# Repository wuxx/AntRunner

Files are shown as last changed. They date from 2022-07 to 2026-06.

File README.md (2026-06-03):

# AntRunner
[中文](./README_cn.md)
 * [Introduce](#introduce)
 * [Feature](#feature)
 * [Specification](#specification)
 * [How to Use](#how-to-use)
 * [System Detail](#system-detail)
    * [Gpredict](#gpredict)
    * [Hamlib](#hamlib)
    * [Look4Sat](#look4sat)
    * [SDR#](#sdr)
 * [How to Get One](#how-to-get-one)
 * [Reference](#reference)

## Introduce
AntRunner is a portable antenna rotator designed and made by MuseLab(Another model we designed is the [AntRunner-Pro](https://github.com/wuxx/AntRunner-Pro), which is suitable for fixed installation and long-term operation). It can be used for real-time automatic racking of satellites with corresponding open source software which is available on Windows/Linux/Mac/RaspberryPi/Android. The rotator and the host computer can communicate via wired (serial port) or wireless (Wifi 2.4G).  It can install various types of antennas (usually Yagi antennas), support 360-degree azimuth and 180-degree elevation control, and can support antennas up to 5KG.  It can be powered by a 12V battery or by a fast charging power bank with a 12V fast charging trigger cable. It’s easy to carry as its weight is relatively light and very convenient to use in the wild for HAM.

AntRunner-1
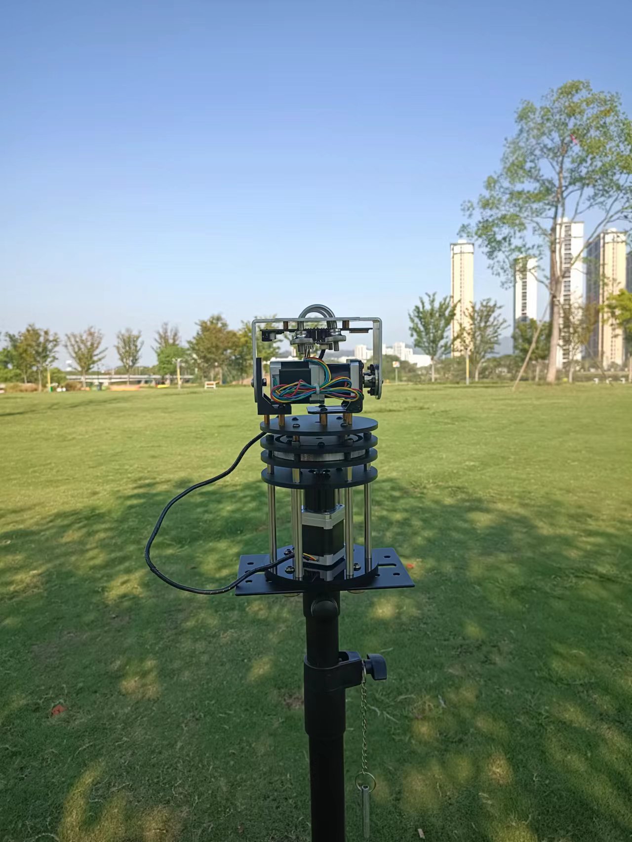
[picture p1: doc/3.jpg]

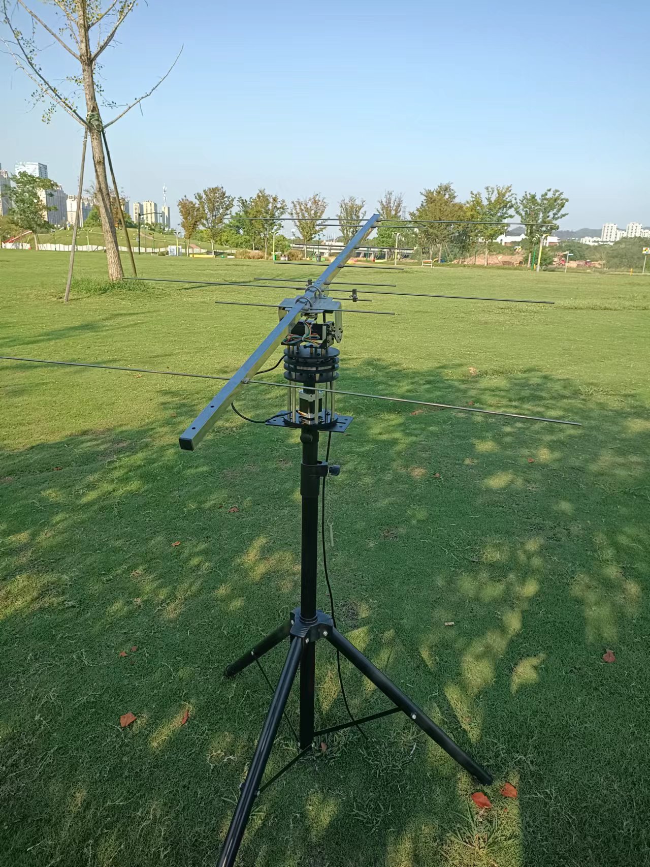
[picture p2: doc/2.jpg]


## Feature
- full Azimuth and elevation angle tracking
- Support Windows/Linux/RaspberryPi/Android
- Support wired serial port control
- Support wireless WiFi 2.4G control
- 12V power supply, convenient for field erection
- Easy disassembly and assembly

## Specification
- Rotation Limit: AZ: 0 - 360°; EL: 0-180°
- Max Load: 5KG
- Backlash: AZ:1° EL:1°
- Weight: 3KG
- Rotator Diameter x Height:  120mmØ x 65mm (H)
- Support Material: 5mm/10mm Acrylic

## How to Use

### Windows

#### 0 Antenna installation
Install the antenna on the U-shaped bracket of the rotator through the U-shaped hoop, and pay attention to install it at the center of gravity of the antenna to make the operation more stable.

#### 1 Rotator adjustment
Before powering on, you need to adjust the azimuth of the rotator to true north (azimuth angle of 0 degrees), and the pitch to be horizontal (pitch angle of 0 degrees). This step can be adjusted through the mobile compass APP.

#### 2 Power up
Use the 12V power supply to power on the rotator, and connect the rotator and PC through the TYPE-C cable. After the normal connection, a serial port will appear in the device manager, as shown in the figure.
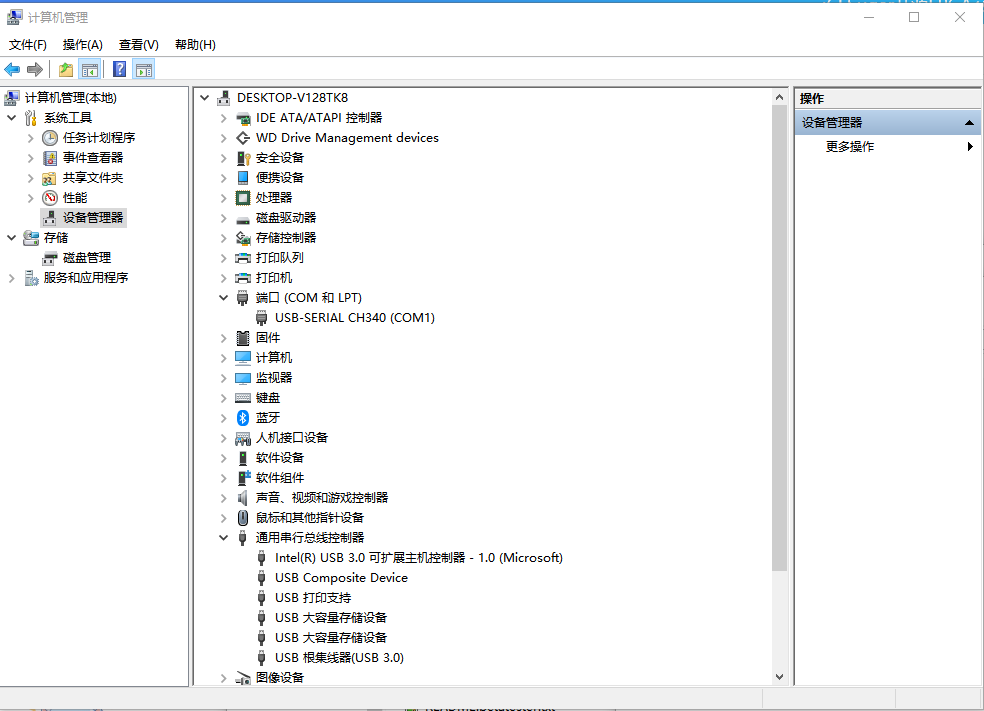
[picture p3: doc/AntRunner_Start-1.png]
AntRunner-1


#### 3 Start Hamlib
Enter the Hamlib directory, there is a batch script in the directory, and the script is a command, as shown below, you need to manually edit the script to modify the serial port number. Since the serial port number is assigned by the system, the serial number is different for different systems, so you need to use a text editor to manually change the serial port number before running.
```
rotctld.exe -vvvvv -m 2401 -r COMx
```
Modify COMx to the actual serial port number that appears in the device manager, save the script, and double-click to run it.
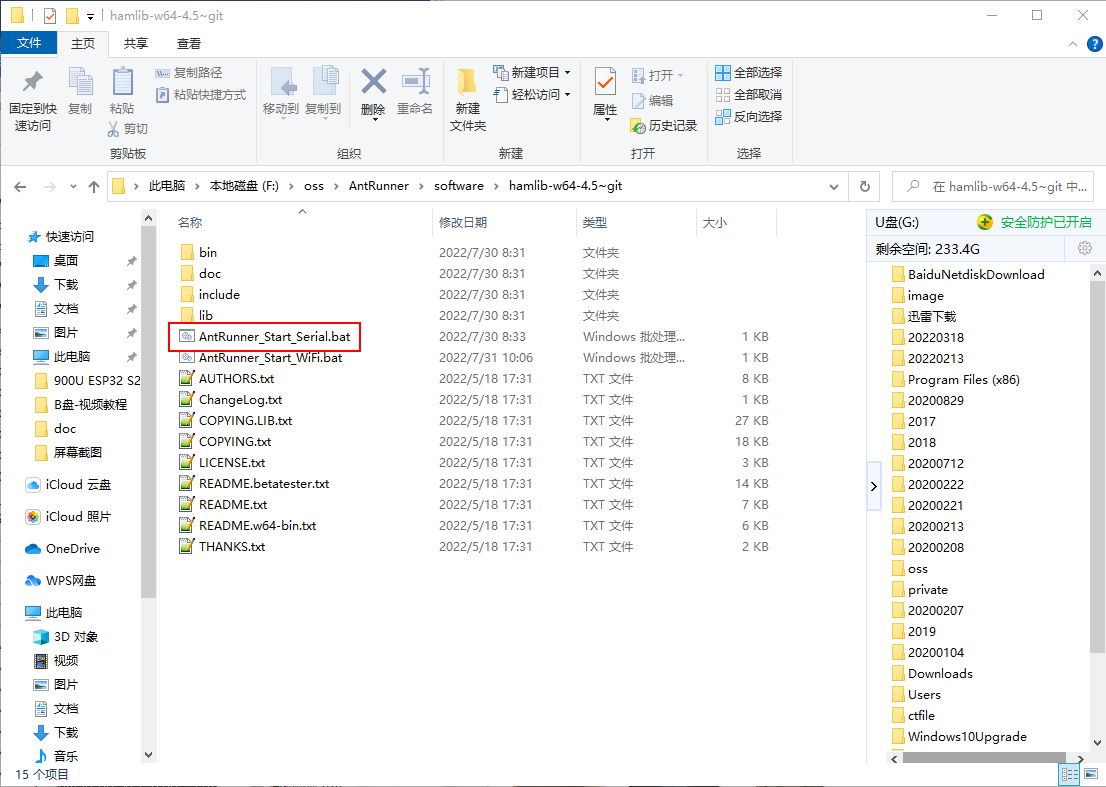
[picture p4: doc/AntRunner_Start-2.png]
AntRunner-2

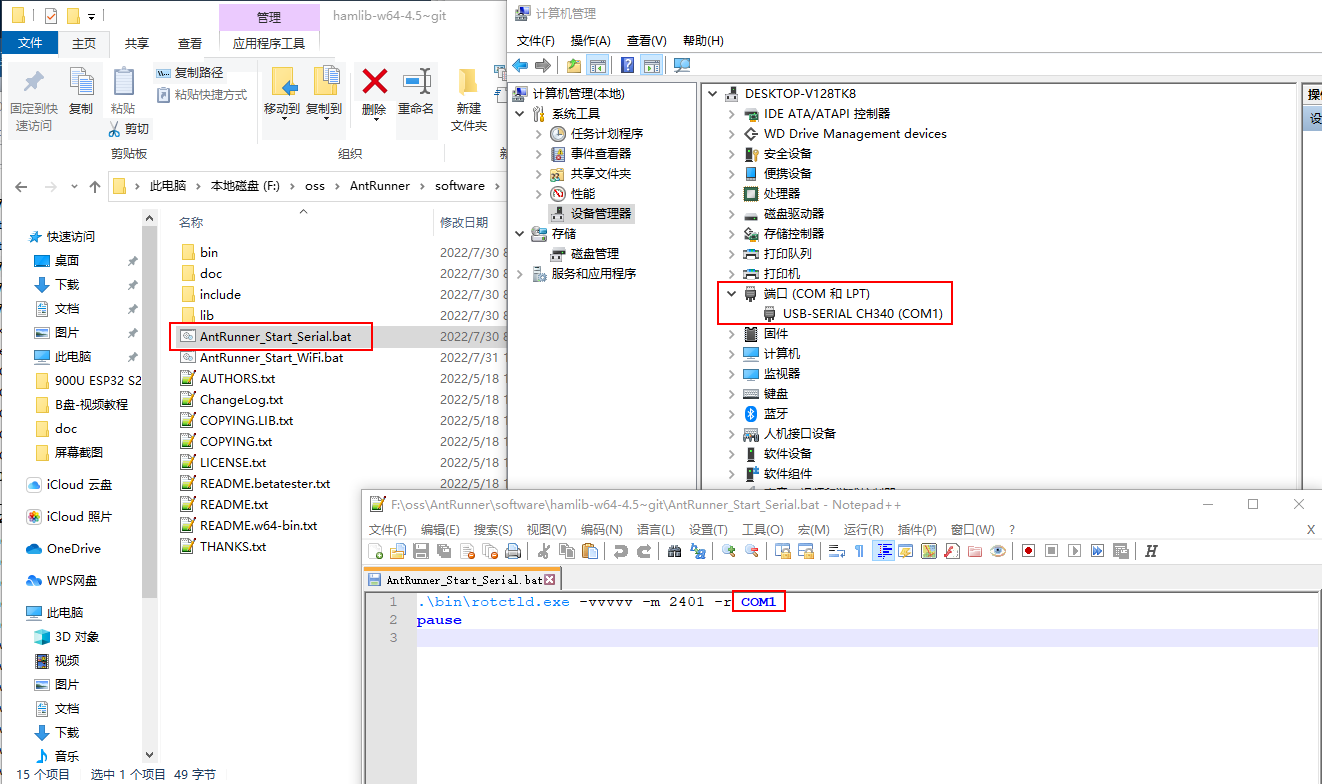
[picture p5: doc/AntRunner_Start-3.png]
AntRunner-3

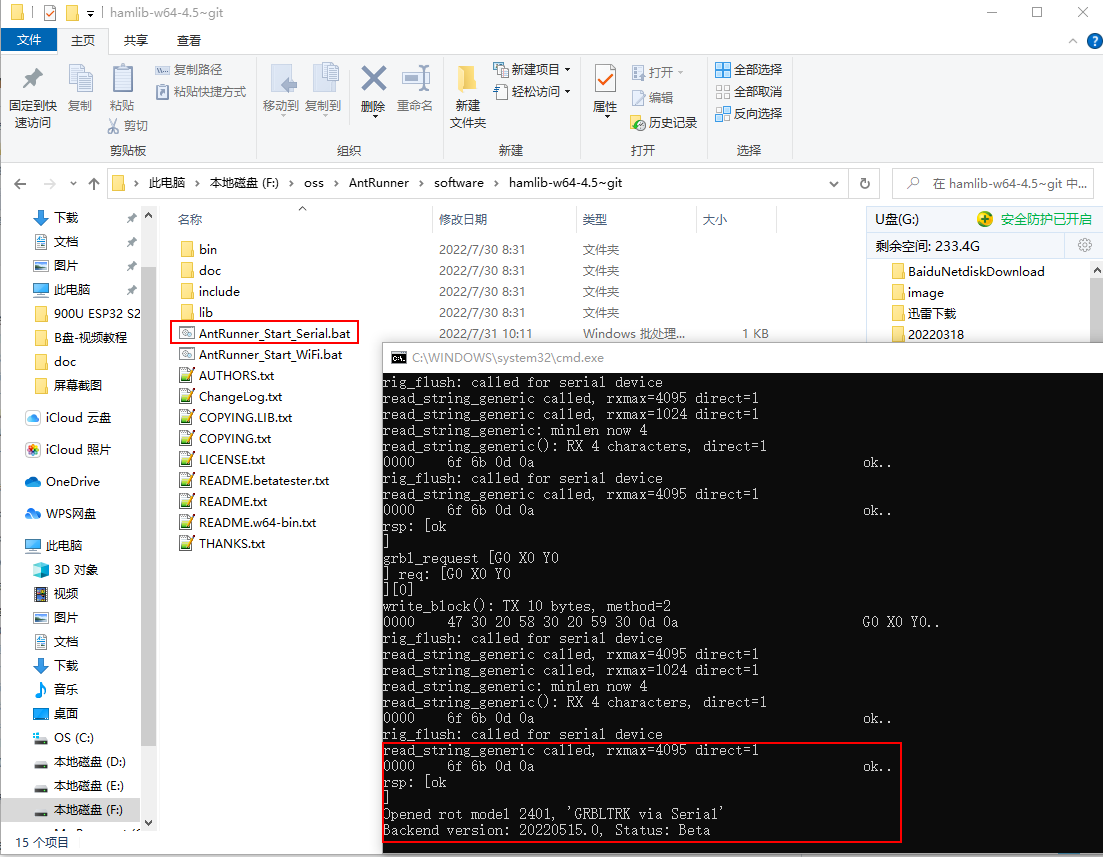
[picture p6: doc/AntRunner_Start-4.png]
AntRunner-4


#### 4 Start Gpredict
Double-click gpredict.exe to open the Gpredict program

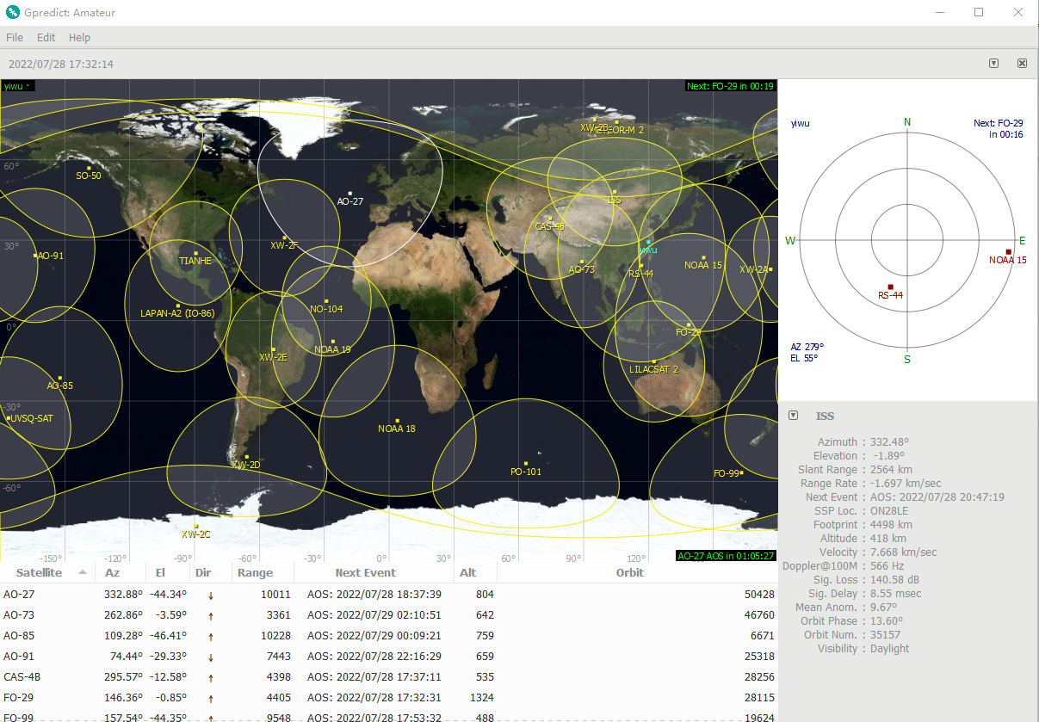
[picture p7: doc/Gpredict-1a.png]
Gpredict-1a


##### 4.1 Longitude and latitude configuration
First, you need to configure the latitude and longitude of your region, select Edit -> General -> Ground Stations -> Add new, and configure your local latitude, longitude and altitude on the page that comes out.
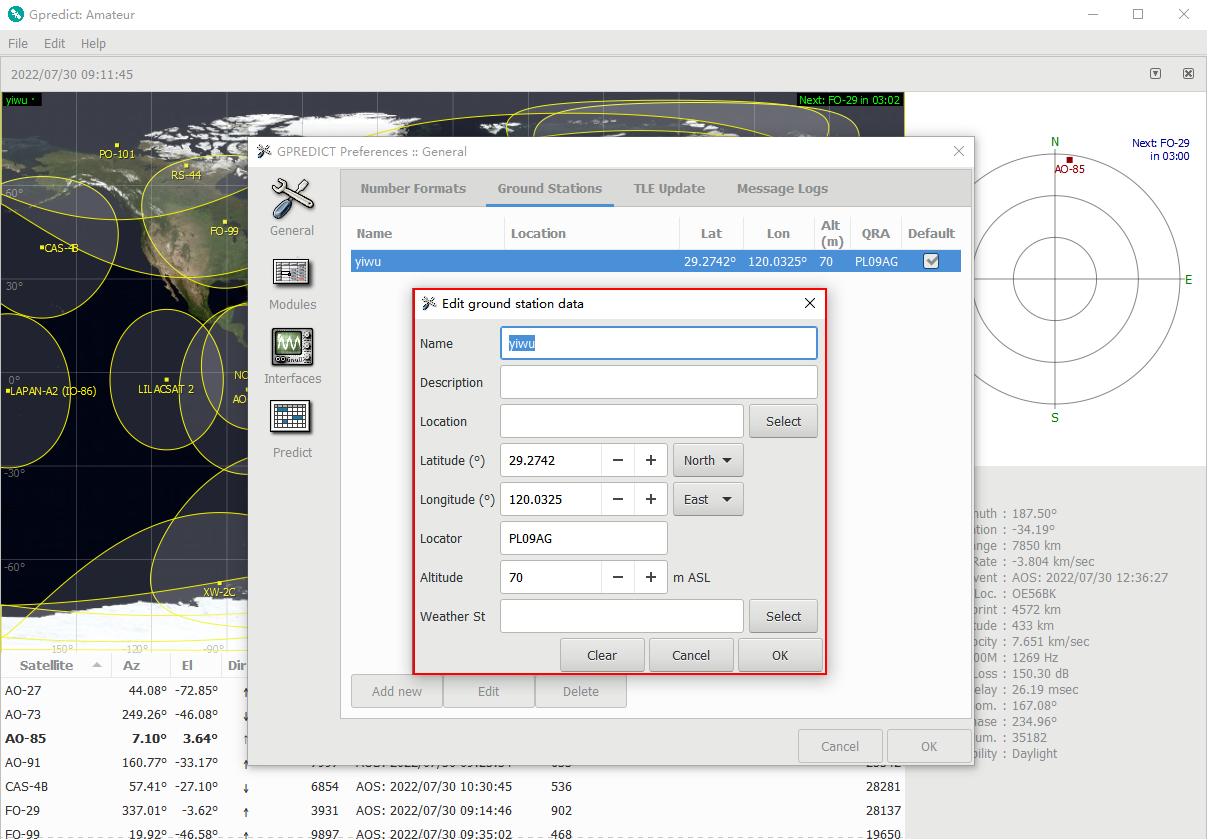
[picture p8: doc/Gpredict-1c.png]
Gpredict-1c


##### 4.2 Satellite configuration
You need to add the satellites you want to track to the list, click the inverted triangle on the upper right, select Configure, and add the satellites you want to track to the small window on the right in the window that appears.
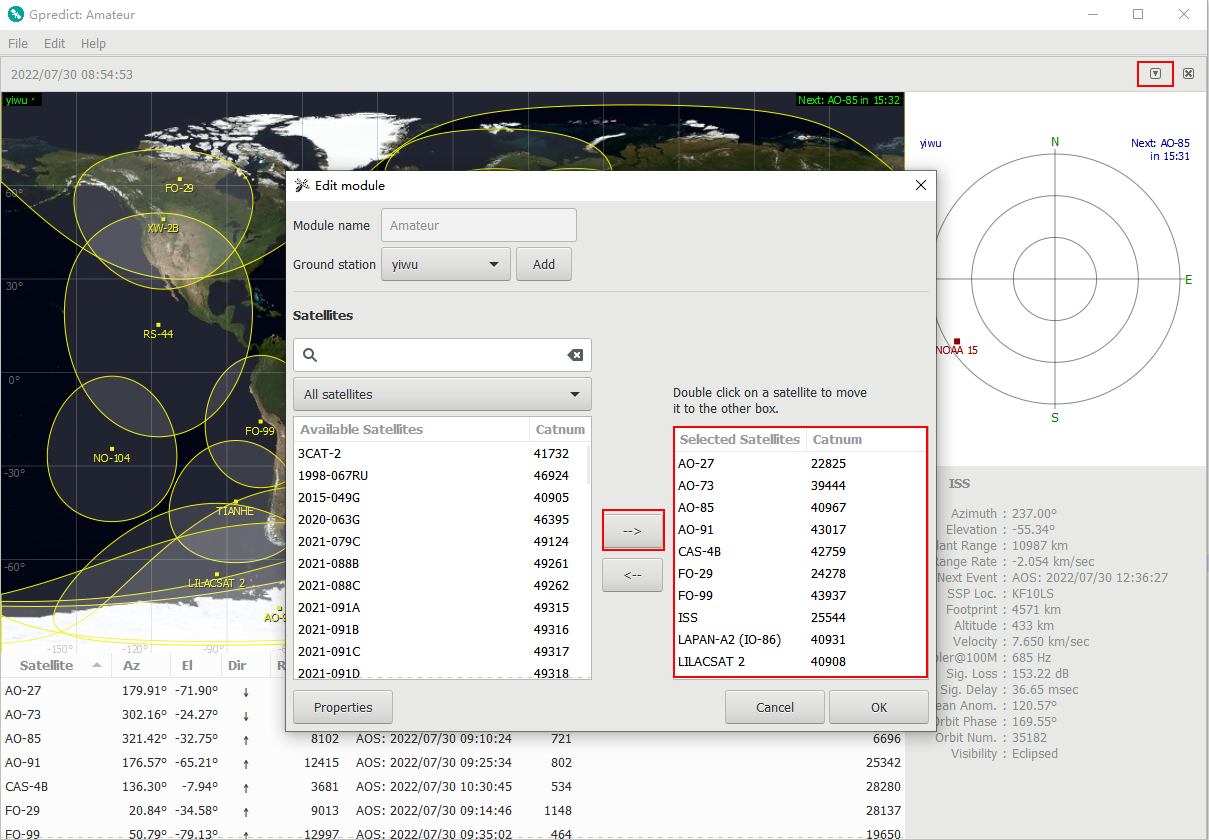
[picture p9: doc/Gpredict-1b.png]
Gpredict-1b


##### 4.3 Rotator configuration
Create a new rotator device, select Edit -> Interfaces -> Rotators -> Add New, and configure it as shown
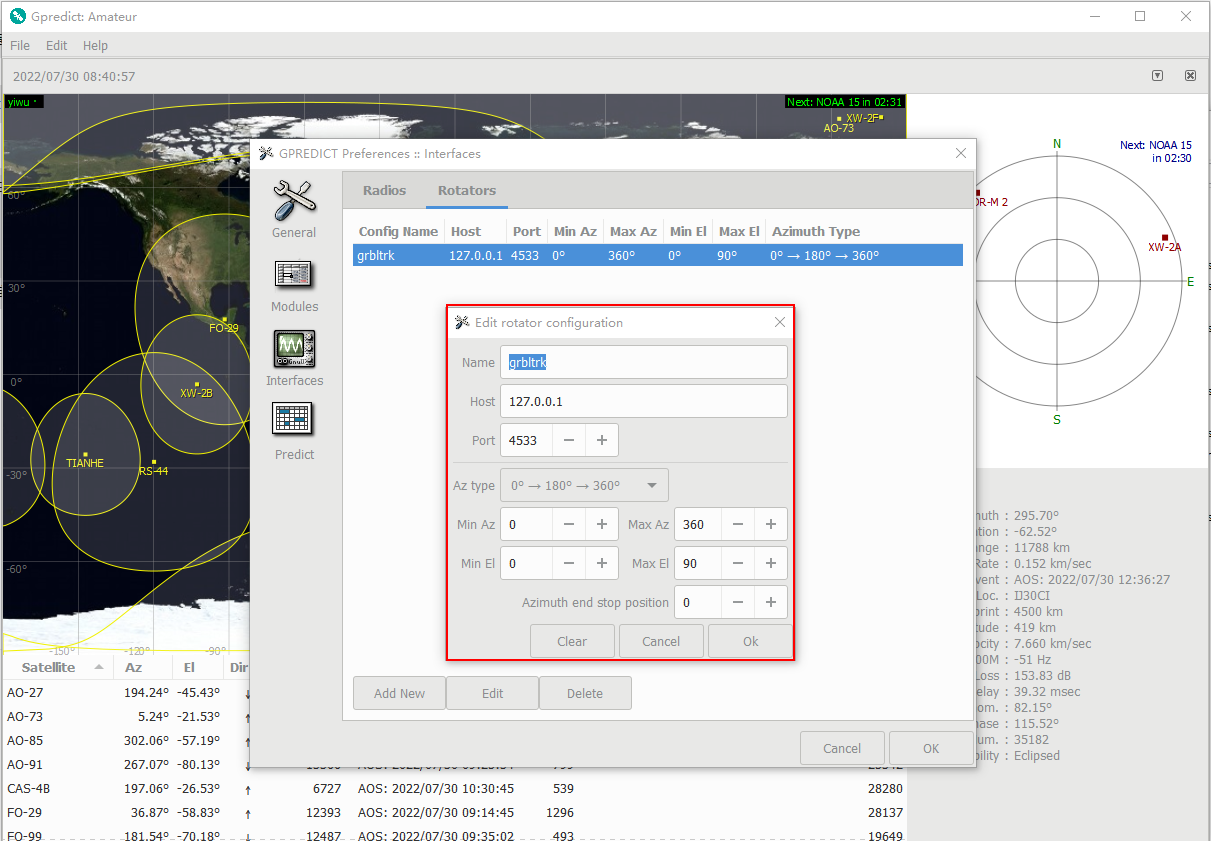
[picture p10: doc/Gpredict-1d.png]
Gpredict-1d


##### 4.4 Rotator test
After configuring the rotator device, you can perform a preliminary test on the rotator. Click the inverted triangle on the upper right and select Antenna Control to enter the antenna control page.
select the newly created grbltrk, click Engage to initialize the rotator, and then configure the azimuth and pitch angles. After configuring the rotator, it will respond immediately and return the current angle value in real time.
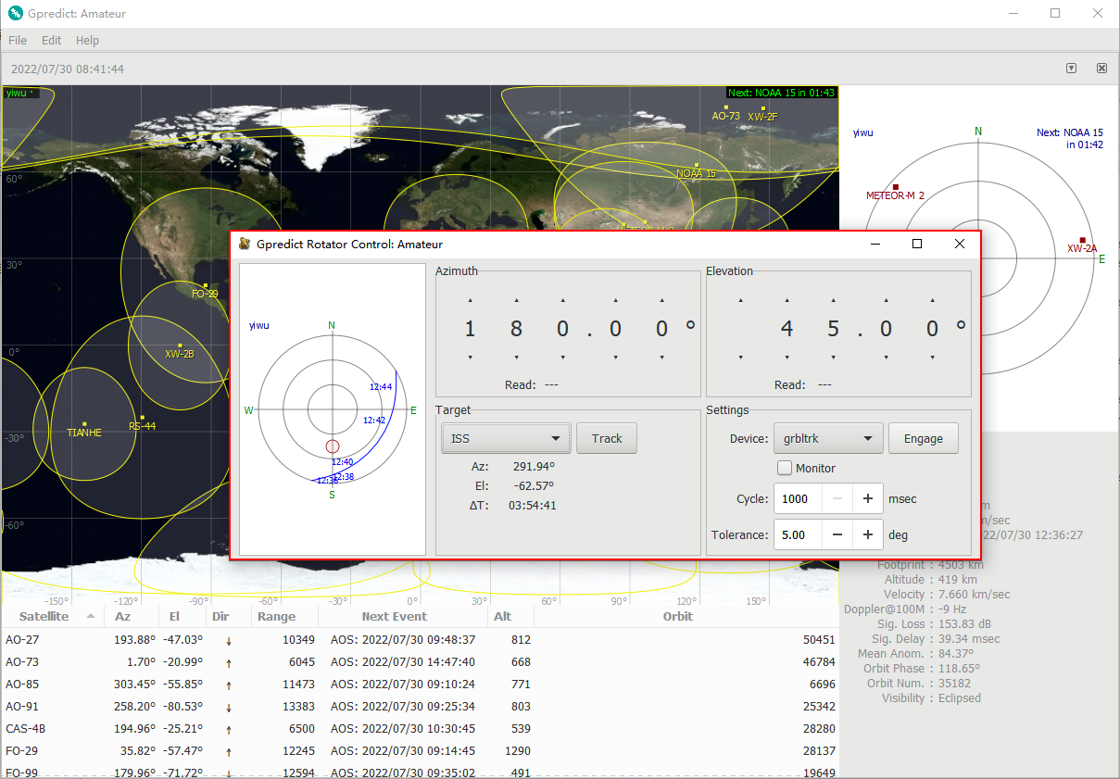
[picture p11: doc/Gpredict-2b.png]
Gpredict-2b

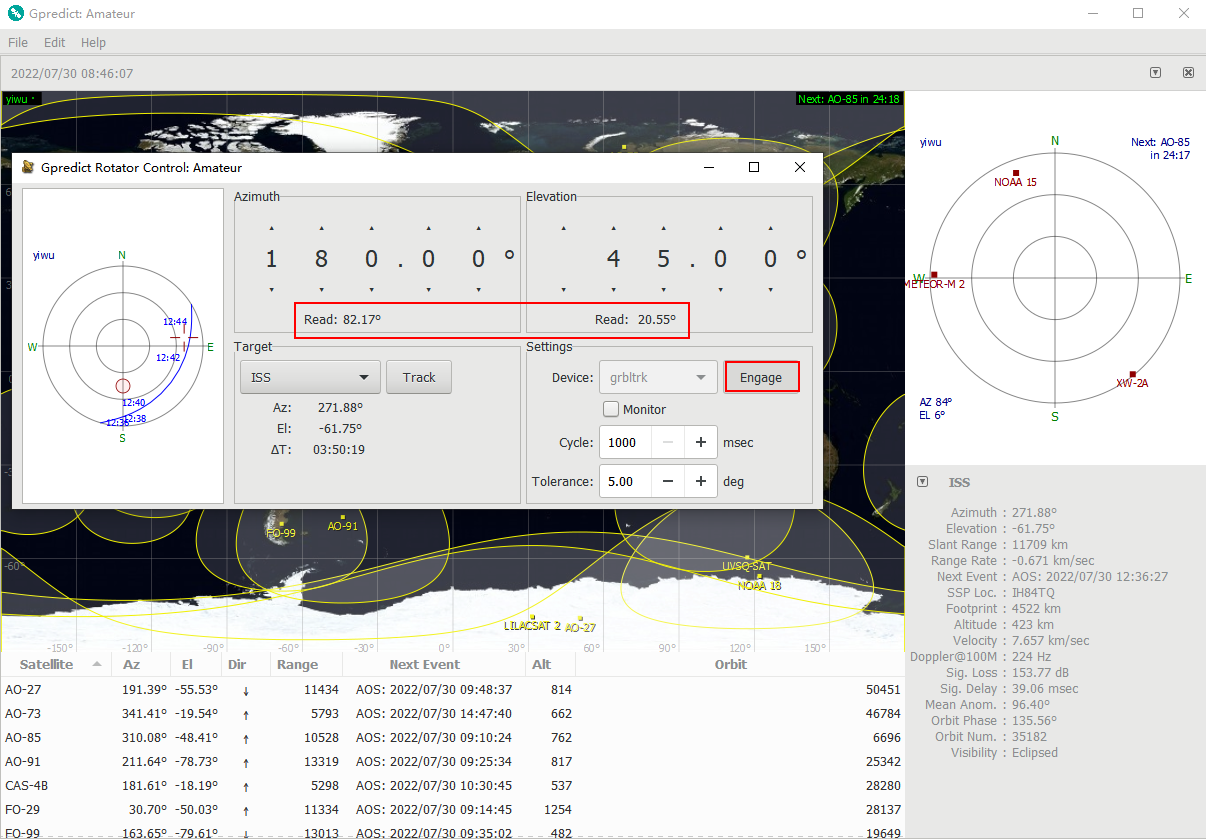
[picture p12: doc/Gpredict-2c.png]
Gpredict-2c

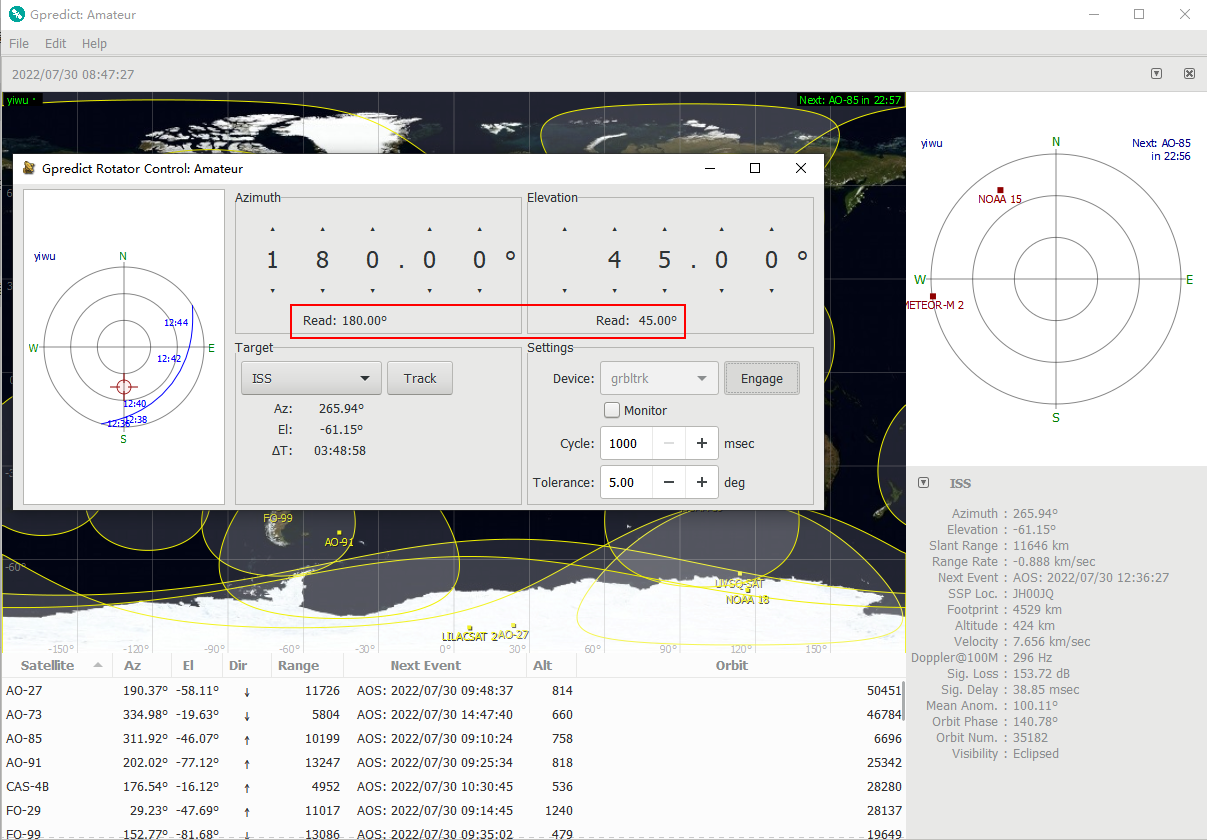
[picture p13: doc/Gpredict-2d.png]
Gpredict-2d


##### 4.5 satellite tracking
Select the satellite to be tracked in Target, such as ISS, click Track, the rotator will start tracking the satellite in real time, if the satellite is not in entry, it will adjust the pitch angle to 0 degrees, and the azimuth angle to the angle when the satellite enters, wait for the satellite to enter, The radar map on the left also shows the satellite's inbound trajectory and the current rotator position.
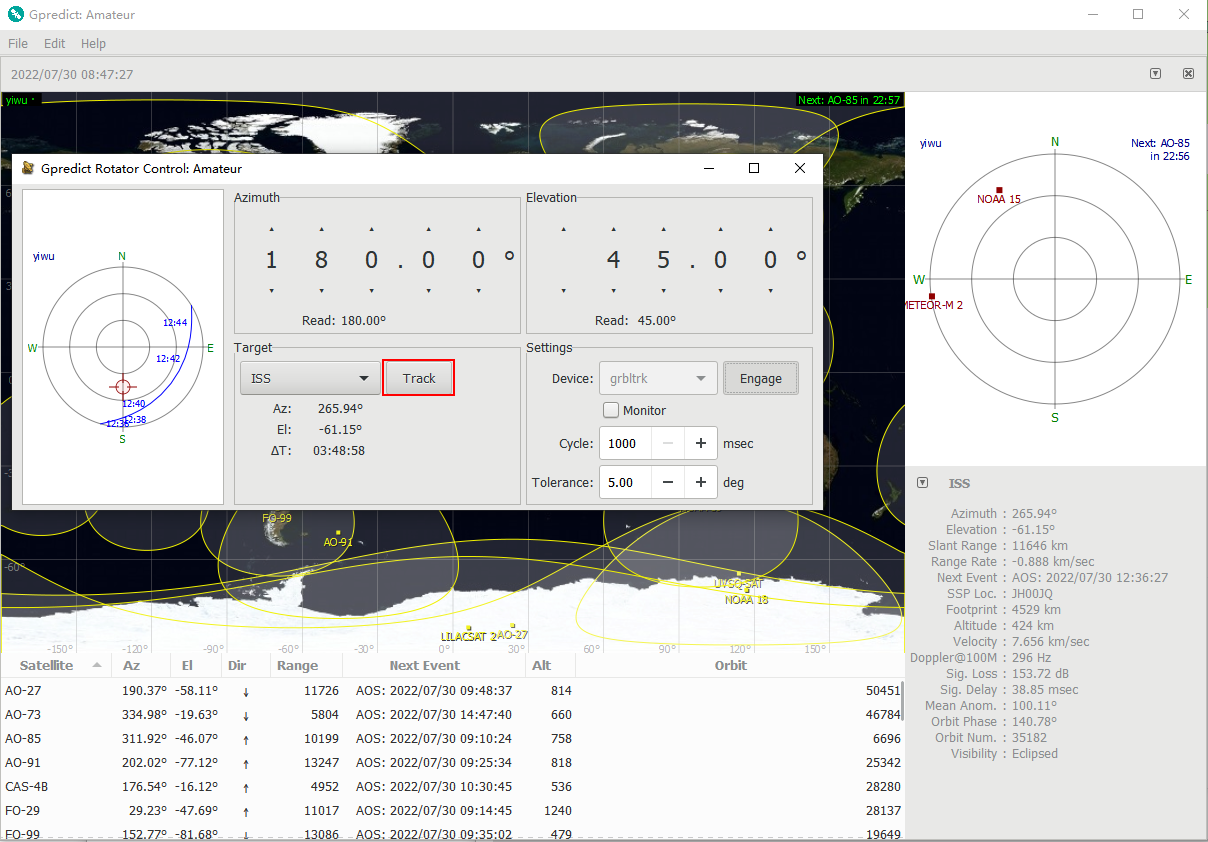
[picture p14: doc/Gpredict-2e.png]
Gpredict-2e

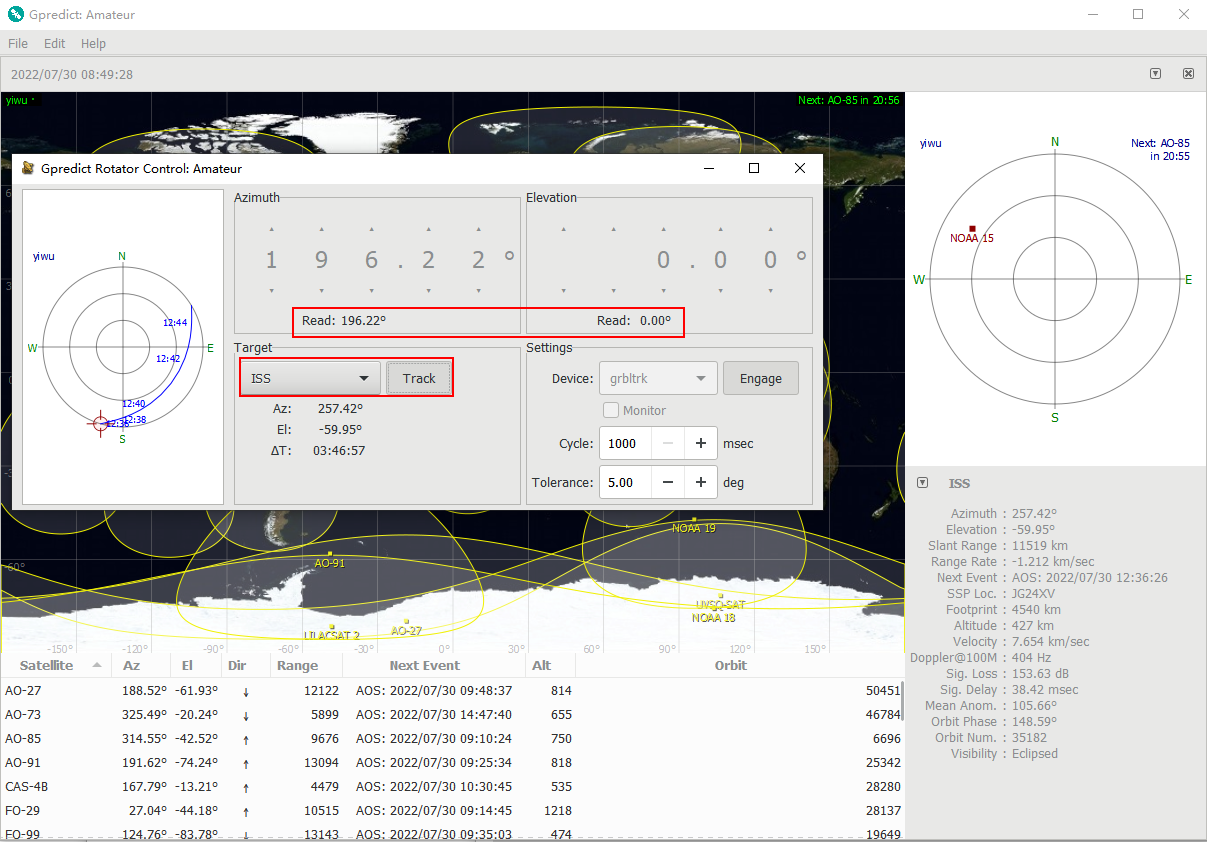
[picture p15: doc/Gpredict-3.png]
Gpredict-3


### Raspberry
Since Gpredict is also supported under Linux, it can be directly run and used in the Raspberry Pi. The operation steps are basically the same, and will not be repeated here.
here is how to start the Hamlib
```
rotctld -vvvvv -m 2401 -r /dev/ttyUSB0
```

### Android
#### Look4Sat 
Look4Sat wireless control is currently supported, please refer to this repo [Look4Sat-AntRunner-Controller](https://github.com/wuxx/Look4Sat-AntRunner-Controller)

## System Detail
This section is a detailed description of the technical principle. Those who are not interested can ignore the description in this section and go directly to the actual operation chapter.

### Rotator Motor Control 
The bottom chip of the rotary controller uses ESP32, and the firmware running on it is GRBL, which was originally an open source CNC control firmware, and was first run on the ATmega328P chip (a low-end single-chip microcomputer with a main frequency of only 16MHz, SRAM The capacity is 2KB, and the Flash storage capacity is 32KB), while ESP32 is a WiFi chip launched by Espressif Information Technology. With 40nm process, dual-core 32-bit MCU, 2.4GHz dual-mode Wi-Fi and Bluetooth chip, the main frequency is up to 240MHz, the SRAM capacity is 520KB, and the Flash capacity is up to 16MB. It supports more and stronger features, so the [Grbl_ESP32 version](https://github.com/bdring/Grbl_Esp32) transplanted by the open source community is used.

It not only supports conventional serial port control, but also has a complete set of WEBUI, which can be manually controlled and configured through the WEBUI, and can also be controlled through the telnet 22 port. (Of course, an HTTP request can also be constructed to realize control from the WEB 80 port), since ESP32 supports Bluetooth, the motor control can also be achieved theoretically through Bluetooth. Since WiFi communication is more universal, the speed and stability of communication are also relatively high. Better, and the software protocol stack based on TCP/IP makes communication more stable and reliable, so the current implementation of wireless control is based on WiFi.

By default it creates its own wireless network SSID `GRBL_ESP` with default password `12345678` you can connect. You can connect and use WebUI to change, or you can change through serial commands to e.g. connect to your existing WiFi network. See the [Grbl_Esp32 wiki](https://github.com/bdring/Grbl_Esp32/wiki/Setting-up-the-Wifi-Network) for more instructions.

Note 1: The control command of the Grbl system is generally called G-code, which is a simple command system also used for e.g. CNC or 3D printing. For example: "G0 X0 Y5" means to move the current position to the coordinates [0mm, 5mm]. But with AntRunner [360º = 40mm](https://github.com/Hamlib/Hamlib/blob/e9fb733dae0e7acb2897850787ebbdcf2520e37c/rotators/grbltrk/grbltrk.c#L220) (both X Azimuth and Y Elevation), so to move to 45º elevation `G0 Y5` or to move azimuth by one degree `G91 G0 X0.111 G90` (relative and then restore absolute).

Grbl also has its own `$…` command system. For more:

* [Grbl FAQ for G-Code](https://github.com/gnea/grbl/wiki/Frequently-Asked-Questions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) points to http://linuxcnc.org/docs/html/gcode.html
* Grbl `$…` commands: https://github.com/gnea/grbl/wiki/Grbl-v1.1-Commands
* Grbl ESP32 has additional settings: https://github.com/bdring/Grbl_Esp32/wiki/Settings

### Gpredict 
Gpredict (https://github.com/csete/gpredict) is lead by Alexandru Csete (call sign oz9aec) is an open source real-time satellite tracking and orbit forecasting software that can track an unlimited number of satellites and display their positions and other data in lists, tables, maps, radars, etc. It can also predict the future time through a satellite and provide you with detailed information. In addition, it can connect to a variety of commonly used radio stations, SDR equipment and a variety of antenna rotators. The main use scenario of AntRunner is to cooperate with Gpredict. Real-time tracking control.
Since it is an open source project based on GPL, Gpredict is still developing under the impetus of the community, and it is believed that more functions and more convenient features will be implemented in the future.

### Hamlib 
Hamlib (https://hamlib.github.io/) is a control library for radios and rotators based on the LGPL open source protocol, supporting Windows/Linux. Gpredict mentioned above can control various types of radio equipment and rotators. The above are all controlled by Hamlib. It can be understood that Hamlib is the middle layer between Gpredict and the actual hardware. Hamlib provides a unified control interface to Gpredict, and itself realizes the operation of complex hardware devices. In actual operation, Hamlib runs in the background as a separate task, which receives requests and sends responses through TCP port 4533. For example: Gpredict sends "p 30 60" through TCP port 4533, which means to adjust the current rotator azimuth to 30 degrees, the pitch angle is adjusted to 60 degrees, and the actual hardware operation is performed by Hamlib. Gpredict does not need to care what type of rotator is used, just specify the model of the rotator when Hamlib starts.
Note: AntRunner's driver is implemented in Hamlib, and has been incorporated into the official Hamlib repository (https://github.com/Hamlib/Hamlib), merge node: https://github.com/Hamlib/Hamlib/pull/1032. Just take the latest version of Hamlib or any release [version 4.5](https://github.com/Hamlib/Hamlib/releases/tag/4.5) or later.

### Look4Sat
Look4Sat (https://github.com/rt-bishop/Look4Sat) is an Android-based open source satellite tracking software implemented by Arty Bishop. The page is concise and easy to use. The latest submission also supports the control of the rotator. The real-time display of the gyroscope is supported during the tracking process, which can easily align the satellite. At present, other similar satellite prediction software does not support this simple use method, and it is widely used in the current HAM.
Look4Sat's control of the rotator is sent over the network, for example "\set_pos 30.0 60.0" means to adjust the current spinner azimuth to 30 degrees and pitch to 60 degrees.
Since Hamlib is not currently supported on the Android side, an additional hardware device is required to control through Look4Sat. Here, I designed a small system based on ESP32-C3 to convert network requests into actual GRBL commands and send them to the GRBL firmware to achieve orientation and The control of pitch is equivalent to implementing a simple "Hamlib" by itself. check the project here [Look4Sat-AntRunner-Controller](https://github.com/wuxx/Look4Sat-AntRunner-Controller)

### SDR#
SDR# is a popular SDR control application. It is simple and convenient to use. It supports a variety of common SDR devices, supports a variety of plug-in functions, and can be linked with Gpredict. At the same time, Gpredict can also support wireless devices and rotators. : Use SDR equipment such as RTL-SDR, and use Gpredict to track satellites at the same time, gpredict can send Doppler frequency to SDR# through the corresponding plug-in in SDR# for real-time adjustment, and Gpredict can control the rotator in real time for tracking. Other plug-ins in SDR# can analyze and record the received signal waveform to realize the linkage of the whole system.

### How to Get One
Some guys ask me if they could buy AntRunner rotator, so I made some AntRunner prototypes. Interested friends can place an order in my tindie store: https://www.tindie.com/products/johnnywu/the-antrunner-rotator/

## Reference
- Gpredict (https://github.com/csete/gpredict) 
- Hamlib (https://hamlib.github.io/)
- Look4Sat (https://github.com/rt-bishop/Look4Sat)
- sdr# (https://airspy.com/download/)
- Look4Sat-AntRunner-Controller (https://github.com/wuxx/Look4Sat-AntRunner-Controller)

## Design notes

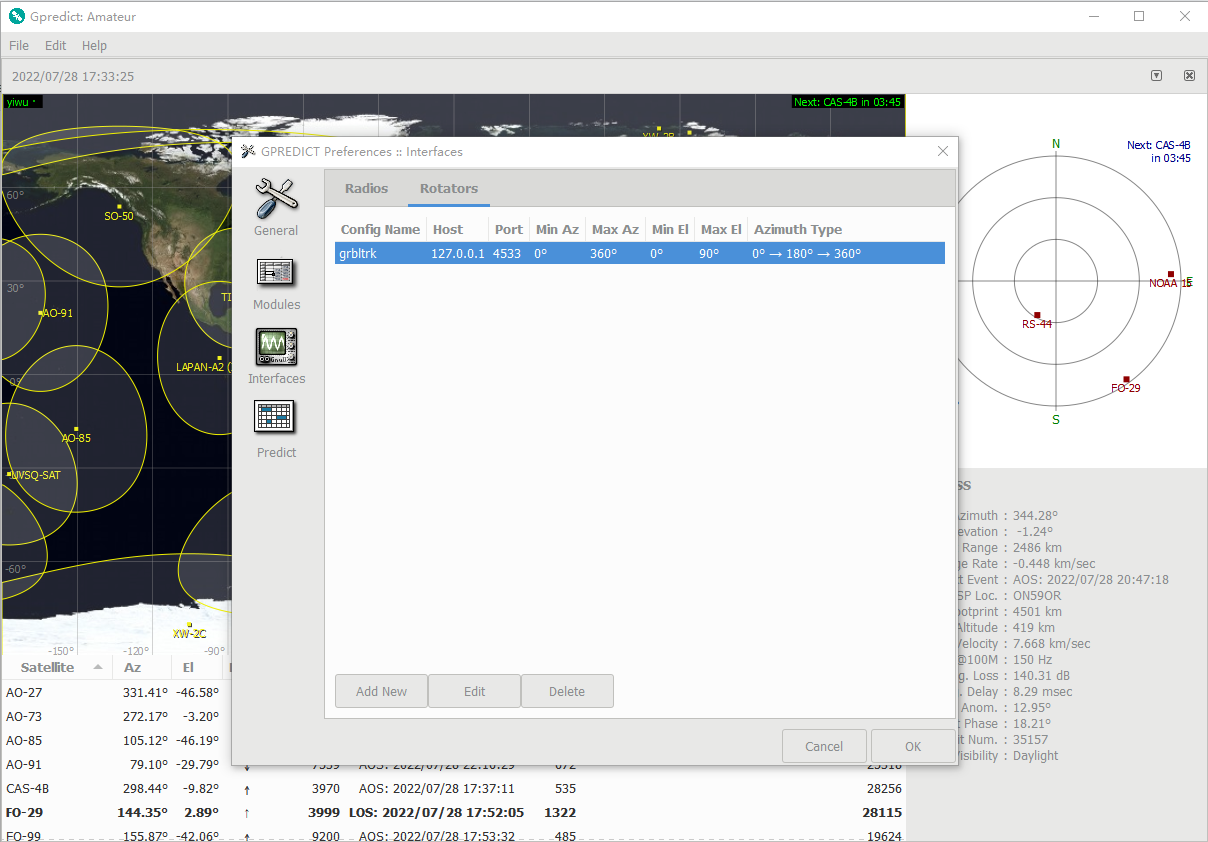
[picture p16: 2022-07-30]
doc/Gpredict-1e.png

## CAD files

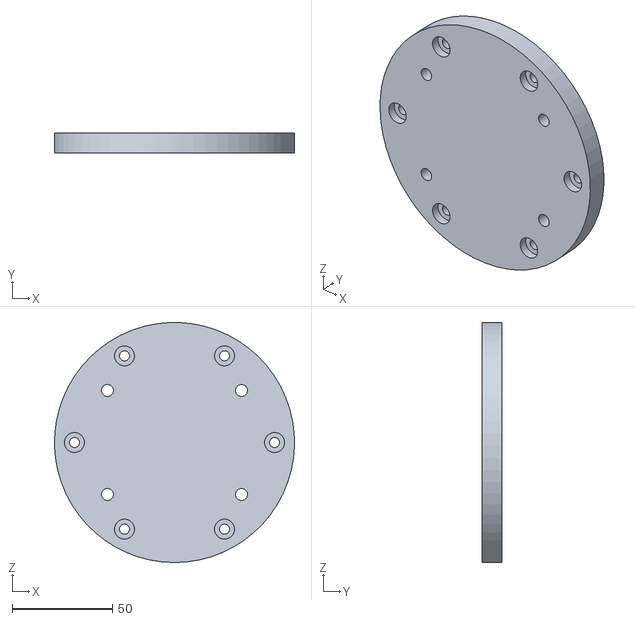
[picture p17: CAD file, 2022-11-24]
structure/Rotator-Bottom-v0.2.STL
120.0 x 10.0 x 120.0

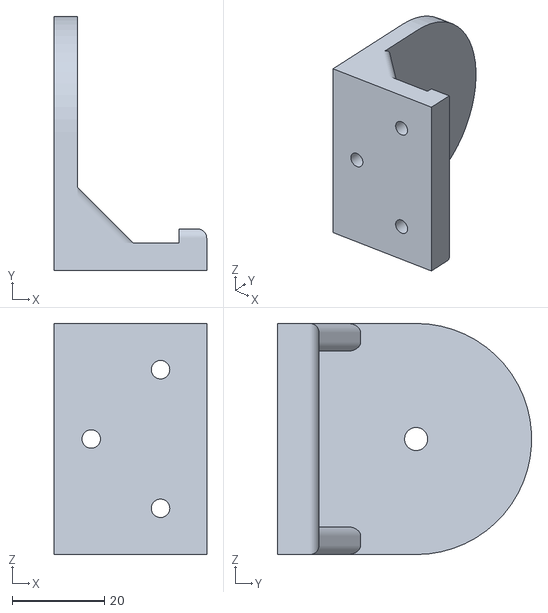
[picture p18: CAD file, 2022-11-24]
structure/L-Bracket-42-v1.2.STL
33.0 x 55.0 x 50.0

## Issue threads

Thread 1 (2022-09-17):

Add license information

vazhnov, 2022-09-17:
Hello!

I found this project from https://hackaday.com/2022/09/17/antrunner-is-the-satellite-antenna-mount-you-need-to-take-with-you/

Could you please add information about the license of this repository — is it allowed to copy, change and use the code and images in any purpose?
It would be great to see any popular open source license.

wuxx, 2022-09-18:
Hello, I will add the license later, and more documents will commit, please wait.

vazhnov, 2022-09-27:
GPL-3.0 license — great! Thank you!

Closed 2022-09-27.

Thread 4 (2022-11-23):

Provide Grbl ESP32 build configuration?

natevw, 2022-11-23:
The default settings of the controller can be accessed from serial and also are copied into: <https://github.com/Hamlib/Hamlib/blob/e9fb733dae0e7acb2897850787ebbdcf2520e37c/rotators/grbltrk/grbltrk.c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> And some version info can be requested over serial with`$I` command.

But can you provide compile-time settings for Machine configuration headers, how to build firmware bin provided here?

wuxx, 2022-11-24:
hello, already commit the source code
https://github.com/wuxx/AntRunner/blob/master/software/Grbl_Esp32-master.zip

natevw, 2022-11-25:
Okay, yes I see now! 👍

Closed 2022-11-25.

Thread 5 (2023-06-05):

Elevation offset by 18 deg

rbadsi, 2023-06-05:
Hi,

It seems that the elevation is always offset by 18 degrees (both in GPredict and when issuing commands directly to rotctl):

```
Rotator command: P 0 40
Azimuth: Elevation: rot_set_position called az=0.00 el=40.00
rot_set_position: south_zero=0
grbltrk_rot_set_position: (prev_x) = (0.000); (prev_az) = (0.000); (prev_el) = (20.000); (curr_az, curr_el) = (0.000, 40.000)
grbltrk_rot_set_position:283 prev_x: 0.000
min_index: 1; curr_x: 0.000
req: [G0 X0.000 Y4.444
][0]
write_block(): TX 17 bytes, method=2
0000    47 30 20 58 30 2e 30 30 30 20 59 34 2e 34 34 34     G0 X0.000 Y4.444
0010    0a                                                  .       
read_string_generic(): RX 4 characters, direct=1
0000    6f 6b 0d 0a                                         ok..    
rsp: [ok
]

Rotator command: p
rot_get_position called
grbltrk_rot_get_position called
req: [?
][0]
write_block(): TX 3 bytes, method=2
0000    3f 0d 0a                                            ?..     
read_string_generic(): RX 44 characters, direct=1
0000    3c 49 64 6c 65 7c 4d 50 6f 73 3a 30 2e 30 30 30     <Idle|MPos:0.000
0010    2c 36 2e 34 34 34 2c 30 2e 30 30 30 7c 46 53 3a     ,6.444,0.000|FS:
0020    30 2c 30 7c 50 6e 3a 58 59 3e 0d 0a                 0,0|Pn:XY>..
0000    6f 6b 0d 0a 6f 6b 0d 0a                             ok..ok..
rsp: [<Idle|MPos:0.000,6.444,0.000|FS:0,0|Pn:XY>
]
grbltrk_rot_get_position: (az, el) = (0.000, 57.996)
rot_get_position: got az=0.00, el=58.00
Azimuth: 0.00
Elevation: 58.00
```

Is this something that can be adjusted somewhere?

Thanks!

wuxx, 2023-06-06:
Hello, please check, if it may be that the bracket is loose

Closed 2023-08-26.

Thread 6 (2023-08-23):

AntRunner Rotation @ 50% of Expected

Splintershop, 2023-08-23:
Angular rotation of motor is only half of what it should be. For example, when 90deg is entered, the motor only rotates half that amount (45deg).  This is true on both azimuth and elevation.  I went so far as to remove all brackets and fittings from the elevation motor to confirm it wasn't a loose set screw or other binding.
This is on a purchased AntRunner.  This is the first setup of the device.  I have tried removing device and device driver, rebooting, anything obvious I could think of.

Windows 11
Standard AntRunner_Start_Serial edited line 1 for Com 3
Gpredict 2.3.37

Suggestions?

wuxx, 2023-08-24:
Hello, can you check if the screw is loose?

Splintershop, 2023-08-24:
I don't believe it's mechanical.  With how I tested things, there isn't any screw that could be loose.  As I said in my original post, I disassembled the elevation bracket from the stepper motor.  In other words, this isolated the motor from anything else.  I was monitoring the actual shaft angle with nothing attached to the motor.
The software is sending the correct G code, and GPredict is showing the expected target angle.  GPredict is also displaying the the expected "read" value.  However, the physical results appear to be scaled by 50%.  I want to repeat that this is with the motor only - it was physically removed from the housing.

wuxx, 2023-08-25:
Hello, there are two motors, are both motors scaled by 50%?

Splintershop, 2023-08-25:
Yes, both the azimuth and elevation motors seem to be scaled.

wuxx, 2023-08-26:
OK... when double click the  AntRunner_Start_Serial.bat, there are many logs, can you send it to me, I will check it.

Splintershop, 2023-08-26:
I need a little more info.  Where would I find the logs?  What directory?  What are the log filenames?

wuxx, 2023-08-26:
when double click the AntRunner_Start_Serial.bat, there is a dos black window, the log is in the window

wuxx, 2023-08-26:
https://github.com/wuxx/AntRunner/blob/master/doc/AntRunner_Start-4.png

Splintershop, 2023-08-26:
Here is the batch file:

.\bin\rotctld.exe -vvvvv -m 2401 -r COM3
::.\bin\rotctld.exe -vvvvv -m 601 -r COM470
pause

And here is the output when the batch file is run:

.\bin\rotctld.exe -vvvvv -m 2401 -r COM3
rotctld, Hamlib 4.5~git Tue May 17 22:03:48 2022 +0000 SHA=468dd1
Report bugs to <hamlib-developer@lists.sourceforge.net>

rot_init called
initrots4_grbltrk: _init called
rot_register (2401)
rot_register (2402)
grbltrk_rot_init:407 rot->caps->rot_model: 2401
set_conf: called
rot_open called
serial_open: COM3
serial_setup: tcgetattr
serial_setup: cfsetispeed=115200,0x1002
serial_setup: cfsetospeed=115200,0x1002
serial_setup: data_bits=8
serial_setup: parity=0
serial_setup: Handshake=None
serial_setup: tcsetattr TCSANOW
read_string_generic called, rxmax=4095 direct=1
grbltrk_rot_open:433 ctrl via serial
req: [$$
][0]
write_block(): TX 4 bytes, method=2
0000    24 24 0d 0a                                         $$..
rig_flush: called for serial device
read_string_generic called, rxmax=4095 direct=1
read_string_generic called, rxmax=1024 direct=1
read_string_generic: minlen now 6
read_string_generic(): RX 6 characters, direct=1
0000    24 30 3d 33 0d 0a                                   $0=3..
rig_flush: called for serial device
read_string_generic called, rxmax=4095 direct=1
0000    24 31 3d 32 35 35 0d 0a 24 32 3d 30 0d 0a 24 33     $1=255..$2=0..$3
0010    3d 33 0d 0a 24 34 3d 30 0d 0a 24 35 3d 31 0d 0a     =3..$4=0..$5=1..
0020    24 36 3d 30 0d 0a 24 31 30 3d 31 0d 0a 24 31 31     $6=0..$10=1..$11
0030    3d 30 2e 30 31 30 0d 0a 24 31 32 3d 30 2e 30 30     =0.010..$12=0.00
0040    32 0d 0a 24 31 33 3d 30 0d 0a 24 32 30 3d 30 0d     2..$13=0..$20=0.
0050    0a 24 32 31 3d 30 0d 0a 24 32 32 3d 30 0d 0a 24     .$21=0..$22=0..$
0060    32 33 3d 33 0d 0a 24 32 34 3d 32 30 30 2e 30 30     23=3..$24=200.00
0070    30 0d 0a 24 32 35 3d 32 30 30 30 2e 30 30 30 0d     0..$25=2000.000.
0080    0a 24 32 36 3d 32 35 30 2e 30 30 30 0d 0a 24 32     .$26=250.000..$2
0090    37 3d 31 2e 30 30 30 0d 0a 24 33 30 3d 31 30 30     7=1.000..$30=100
00a0    30 2e 30 30 30 0d 0a 24 33 31 3d 30 2e 30 30 30     0.000..$31=0.000
00b0    0d 0a 24 33 32 3d 30 0d 0a 24 4e 31 3d 0d 0a 24     ..$32=0..$N1=..$
00c0    4e 30 3d 0d 0a 24 31 30 30 3d 31 37 37 36 2e 30     N0=..$100=1776.0
00d0    30 30 0d 0a 24 31 30 31 3d 31 37 37 36 2e 30 30     00..$101=1776.00
00e0    30 0d 0a 24 31 30 32 3d 31 30 30 2e 30 30 30 0d     0..$102=100.000.
00f0    0a 24 31 31 30 3d 35 30 2e 30 30 30 0d 0a 24 31     .$110=50.000..$1
0100    31 31 3d 35 30 2e 30 30 30 0d 0a 24 31 31 32 3d     11=50.000..$112=
0110    31 30 30 30 2e 30 30 30 0d 0a 24 31 32 30 3d 32     1000.000..$120=2
0120    35 2e 30 30 30 0d 0a 24 31 32 31 3d 32 35 2e 30     5.000..$121=25.0
0130    30 30 0d 0a 24 31 32 32 3d 32 30 30 2e 30 30 30     00..$122=200.000
0140    0d 0a 24 31 33 30 3d 33 30 30 2e 30 30 30 0d 0a     ..$130=300.000..
0150    24 31 33 31 3d 33 30 30 2e 30 30 30 0d 0a 24 31     $131=300.000..$1
0160    33 32 3d 33 30 30 2e 30 30 30 0d 0a 6f 6b 0d 0a     32=300.000..ok..
0170    6f 6b 0d 0a                                         ok..
rsp: [$0=3
]
grbl_request [$1=255
] req: [$1=255
][0]
write_block(): TX 8 bytes, method=2
0000    24 31 3d 32 35 35 0d 0a                             $1=255..
rig_flush: called for serial device
read_string_generic called, rxmax=4095 direct=1
read_string_generic called, rxmax=1024 direct=1
read_string_generic: minlen now 4
read_string_generic(): RX 4 characters, direct=1
0000    6f 6b 0d 0a                                         ok..
rig_flush: called for serial device
read_string_generic called, rxmax=4095 direct=1
0000    6f 6b 0d 0a                                         ok..
rsp: [ok
]
grbl_request [$3=3
] req: [$3=3
][0]
write_block(): TX 6 bytes, method=2
0000    24 33 3d 33 0d 0a                                   $3=3..
rig_flush: called for serial device
read_string_generic called, rxmax=4095 direct=1
read_string_generic called, rxmax=1024 direct=1
read_string_generic: minlen now 4
read_string_generic(): RX 4 characters, direct=1
0000    6f 6b 0d 0a                                         ok..
rig_flush: called for serial device
read_string_generic called, rxmax=4095 direct=1
0000    6f 6b 0d 0a                                         ok..
rsp: [ok
]
grbl_request [$100=1776
] req: [$100=1776
][0]
write_block(): TX 11 bytes, method=2
0000    24 31 30 30 3d 31 37 37 36 0d 0a                    $100=1776..
rig_flush: called for serial device
read_string_generic called, rxmax=4095 direct=1
read_string_generic called, rxmax=1024 direct=1
read_string_generic: minlen now 4
read_string_generic(): RX 4 characters, direct=1
0000    6f 6b 0d 0a                                         ok..
rig_flush: called for serial device
read_string_generic called, rxmax=4095 direct=1
0000    6f 6b 0d 0a                                         ok..
rsp: [ok
]
grbl_request [$101=1776
] req: [$101=1776
][0]
write_block(): TX 11 bytes, method=2
0000    24 31 30 31 3d 31 37 37 36 0d 0a                    $101=1776..
rig_flush: called for serial device
read_string_generic called, rxmax=4095 direct=1
read_string_generic called, rxmax=1024 direct=1
read_string_generic: minlen now 4
read_string_generic(): RX 4 characters, direct=1
0000    6f 6b 0d 0a                                         ok..
rig_flush: called for serial device
read_string_generic called, rxmax=4095 direct=1
0000    6f 6b 0d 0a                                         ok..
rsp: [ok
]
grbl_request [$110=50
] req: [$110=50
][0]
write_block(): TX 9 bytes, method=2
0000    24 31 31 30 3d 35 30 0d 0a                          $110=50..
rig_flush: called for serial device
read_string_generic called, rxmax=4095 direct=1
read_string_generic called, rxmax=1024 direct=1
read_string_generic: minlen now 4
read_string_generic(): RX 4 characters, direct=1
0000    6f 6b 0d 0a                                         ok..
rig_flush: called for serial device
read_string_generic called, rxmax=4095 direct=1
0000    6f 6b 0d 0a                                         ok..
rsp: [ok
]
grbl_request [$111=50
] req: [$111=50
][0]
write_block(): TX 9 bytes, method=2
0000    24 31 31 31 3d 35 30 0d 0a                          $111=50..
rig_flush: called for serial device
read_string_generic called, rxmax=4095 direct=1
read_string_generic called, rxmax=1024 direct=1
read_string_generic: minlen now 4
read_string_generic(): RX 4 characters, direct=1
0000    6f 6b 0d 0a                                         ok..
rig_flush: called for serial device
read_string_generic called, rxmax=4095 direct=1
0000    6f 6b 0d 0a                                         ok..
rsp: [ok
]
grbl_request [$120=25
] req: [$120=25
][0]
write_block(): TX 9 bytes, method=2
0000    24 31 32 30 3d 32 35 0d 0a                          $120=25..
rig_flush: called for serial device
read_string_generic called, rxmax=4095 direct=1
read_string_generic called, rxmax=1024 direct=1
read_string_generic: minlen now 4
read_string_generic(): RX 4 characters, direct=1
0000    6f 6b 0d 0a                                         ok..
rig_flush: called for serial device
read_string_generic called, rxmax=4095 direct=1
0000    6f 6b 0d 0a                                         ok..
rsp: [ok
]
grbl_request [$121=25
] req: [$121=25
][0]
write_block(): TX 9 bytes, method=2
0000    24 31 32 31 3d 32 35 0d 0a                          $121=25..
rig_flush: called for serial device
read_string_generic called, rxmax=4095 direct=1
read_string_generic called, rxmax=1024 direct=1
read_string_generic: minlen now 4
read_string_generic(): RX 4 characters, direct=1
0000    6f 6b 0d 0a                                         ok..
rig_flush: called for serial device
read_string_generic called, rxmax=4095 direct=1
0000    6f 6b 0d 0a                                         ok..
rsp: [ok
]
grbl_request [G90
] req: [G90
][0]
write_block(): TX 5 bytes, method=2
0000    47 39 30 0d 0a                                      G90..
rig_flush: called for serial device
read_string_generic called, rxmax=4095 direct=1
read_string_generic called, rxmax=1024 direct=1
read_string_generic: minlen now 4
read_string_generic(): RX 4 characters, direct=1
0000    6f 6b 0d 0a                                         ok..
rig_flush: called for serial device
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
wuxx, 2023-08-26:
OK

Splintershop, 2023-08-27:
Another data point.  I moved the AntRunner from my Windows 10 box to a Raspberry Pi, and am seeing the same behavior.  This should eliminate the PC/PC software as the issue.

Videos to follow.

Splintershop, 2023-08-27:
Video 1 - Elevation change from 0 to 90 and back to 0 degrees.

https://github.com/wuxx/AntRunner/assets/20152721/5e09d7d0-4cfe-4504-8b7e-caea6e13ad97

Splintershop, 2023-08-27:
Video 2 - Azimuth change from 0 to 180 and back to 0.

https://github.com/wuxx/AntRunner/assets/20152721/1c5afe86-c89c-4166-b37a-04cdb34066dd

wuxx, 2023-08-28:
It seems that the motor movement is not normal, and it does not move to 45 degrees. In the first video, it may only be 15 degrees by visual inspection. When it is working normally, the movement is actually relatively smooth.

wuxx, 2023-08-28:
Can you check to see if it might be a lack of power supply?

Splintershop, 2023-08-28:
That was it!  I connected to a very stiff USB-C and it worked flawlessly.  I wondered about that when I was seeing the erratic (not-smooth) movement.  It is now very very smooth, moving to the proper setting accurately.  I am ecstatic!

What is the actual input voltage to the board (wiring in direct versus through the cable that was provided)?

Thank you for staying with me on this.  I'll post a new video tomorrow, demonstrating the correct behavior.

wuxx, 2023-08-28:
The working voltage is 12V, the 12V supplies power to the motor, and a power chip converts 12V into 5V and 3.3V for powering the ESP32 system, can check the schematic for detail.

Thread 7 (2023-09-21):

Other board/card

TREBOR81400, 2023-09-21:
Hello, is it possible to run the AntRunner program on a “MakerFR Grbl 32Bits Board” card, Thank you

wuxx, 2023-09-22:
Hello, board based on ESP32 should be ok

TREBOR81400, 2023-09-22:
thanks I will try.......

TREBOR81400, 2023-09-24:
Hello
I tried to compile AnrRunner on a GRBL 32bits board V2 from MakerFr, the map manager version 1.0.4 does not recognize it, I tried to compile with the latest version, there the card is taken into account but I have an error message like this:
error: cannot convert 'esp_interface_t' to 'wifi_interface_t'
Do you have an idea to compile on my map?
Thank you

Closed 2023-10-03.

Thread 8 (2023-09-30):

Elevation "play" is it normal? I provided a photo. If place my arrow II antenna on the antrunner it tilts about 10 degrees. Worried that is skewing it's ability to track.

curtiswilliams, 2023-09-30:
Also where can I go in and change the azimuth initial rotation occurring?

grbltrk_rot_get_position: (az, el) = (63.000, 0.000)

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

mcules, 2024-08-22:
I had the same problem. There is a second thread in the axis. I inserted a second set screw there. You should tighten both screws regularly. Since then, the play has significantly improved.

wuxx, 2024-08-23:
Generally, the screws are loose. Please tighten them with a hexagonal wrench.

Closed 2025-08-02.

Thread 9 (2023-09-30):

AntRunner Start Wifi.bat

TREBOR81400, 2023-09-30:
hello, could you give me the exact syntax for the "AntRunner Start Wifi.bat" Thank you

wuxx, 2023-10-01:
Hello, this is a dos bat script. You can use a text editor (notepad++ is recommended) to open this bat script for editing. There is only one command in it. Generally, you only need to modify the port number in jthis bat file.

TREBOR81400, 2023-10-01:
Hello, the script for serial is:
.\bin\rotctld.exe -vvvvv -m 2401 -r COMXpause
What is the good script for Wifi, please
Thank you
    Le dimanche 1 octobre 2023 à 03:34:42 UTC+2, wuxx ***@***.***> a écrit :

Hello, this is a dos bat script. You can use a text editor (notepad++ is recommended) to open this bat script for editing. There is only one command in it. Generally, you only need to modify the port number in jthis bat file.

—
Reply to this email directly, view it on GitHub, or unsubscribe.
You are receiving this because you authored the thread.Message ID: ***@***.***>

wuxx, 2023-10-03:
Control based on wifi is currently not supported because wifi may be unstable. It is currently recommended to use a wired serial port for control.

TREBOR81400, 2023-10-03:
Ok Thank You
    Le mardi 3 octobre 2023 à 03:30:32 UTC+2, wuxx ***@***.***> a écrit :

Control based on wifi is currently not supported because wifi may be unstable. It is currently recommended to use a wired serial port for control.

—
Reply to this email directly, view it on GitHub, or unsubscribe.
You are receiving this because you authored the thread.Message ID: ***@***.***>

Closed 2023-10-03.

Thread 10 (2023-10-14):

firmware

TREBOR81400, 2023-10-14:
Good morning,
Can I directly flash the firmware file “flash_image_20220821.bin” onto the universal controller card “6 Pack Universal CNC Controller by Bart Dring of Tindie” to operate an antenna rotator? Will this work directly without modification? THANKS

wuxx, 2023-10-20:
Hello, it probably won’t work. You can refer to the schematic for details.

TREBOR81400, 2023-10-20:
hello, thank you for your response, but I have already, through clumsiness, broken down a card that you kindly resold to me, telling me that it was a small series. I actually wish, as the Tindie site does not offer not a codified replacement card, have an "other" technical possibility to be able to continue using my AntRunner in the event of a new breakdown, particularly on the USB connection which I find fragile. Hence my search for a possible alternative solution. THANKS

    Le vendredi 20 octobre 2023 à 05:27:24 UTC+2, wuxx ***@***.***> a écrit :

Hello, it probably won’t work. You can refer to the schematic for details.

—
Reply to this email directly, view it on GitHub, or unsubscribe.
You are receiving this because you authored the thread.Message ID: ***@***.***>

wuxx, 2023-10-20:
Hello, is the TYPE-C USB interface damaged? You can use an external USB to UART tool to access it.

wuxx, 2023-10-20:
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

wuxx, 2023-10-20:
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

wuxx, 2023-10-20:
Unplug the J5 short-circuit cap and connect it with an external USB to UART tool.

TREBOR81400, 2023-10-20:
thank you but it's too thin to solder for me, it's not easy to find a connector, I would prefer that you put a whole cart for sale as a reference and I will order it from you, ceal will make me a backup card just in case, THANKS

    Le vendredi 20 octobre 2023 à 13:37:12 UTC+2, wuxx ***@***.***> a écrit :

Unplug the J5 short-circuit cap and connect it with an external USB to UART tool.

—
Reply to this email directly, view it on GitHub, or unsubscribe.
You are receiving this because you authored the thread.Message ID: ***@***.***>

wuxx, 2023-10-22:
Okay, please contact us through the platform you purchased

TREBOR81400, 2023-10-22:
thank you, but I don't see the complete electronic card on your Tindie store alone

    Le dimanche 22 octobre 2023 à 02:39:34 UTC+2, wuxx ***@***.***> a écrit :

Okay, please contact us through the platform you purchased

—
Reply to this email directly, view it on GitHub, or unsubscribe.
You are receiving this because you authored the thread.Message ID: ***@***.***>

wuxx, 2023-10-23:
Yes, individual boards cannot work independently, so there is currently no separate link

TREBOR81400, 2023-10-23:
so I was stupid to buy an AntRunner when I can't order spare parts in case of breakdown

    Le lundi 23 octobre 2023 à 03:07:38 UTC+2, wuxx ***@***.***> a écrit :

Yes, individual boards cannot work independently, so there is currently no separate link

—
Reply to this email directly, view it on GitHub, or unsubscribe.
You are receiving this because you authored the thread.Message ID: ***@***.***>

wuxx, 2023-10-24:
It’s no problem to purchase the parts separately, just contact us please.

TREBOR81400, 2023-10-24:
Merci
    Le mardi 24 octobre 2023 à 02:15:34 UTC+2, wuxx ***@***.***> a écrit :

It’s no problem to purchase the parts separately, just contact us please.

—
Reply to this email directly, view it on GitHub, or unsubscribe.
You are receiving this because you authored the thread.Message ID: ***@***.***>

Closed 2025-08-02.

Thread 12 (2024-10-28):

Look4sat ant runner controller problem

HuubH, 2024-10-28:
Hi,

I ordered the Look4sat-AntRunner controller from JLCPCB, I mounted the components, connected the controller to my local wifi and placed it on the AntRunner board.

Look4sat on my android tablet connects to the Look4sat-AntRunner controller and seems to receive data when connected and selecting a satellite in look4sat the Green led starts to blink. When stopping look4sat there is the steady green light so that connection seems fine.

The problem is that Antrunner does not respond at all, no movement or tracking. In normal use Antrunner works fine.

I've used both the ready compiled and also the compiled from source version from Look4sat-AntRunner GIT. Both act the same.

What am I missing? Could you please provide me some guidance.

Much appreciated.

Best regards,
Huub

wuxx, 2025-08-02:
Hello, You need to remove the jumper cap on the control board first to bypass the CH340 serial port chip on the board.

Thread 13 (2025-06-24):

Lots of HF noise up to UHF

df7cb, 2025-06-24:
Hi,

thanks for AntRunner, I like the design a lot!

Unfortunately, I have S9 noise on 2m and S3 on 70cm so I can barely hear the satellites. It seems to be coming from the step motor drivers, when disconnecting the motors, the ESP32 alone is pretty quiet.

Is there any remedy for this? I tried shielding the motor cables, but it only helped on 70cm, 2m is still unusable when the motors are powered.

73,
Christoph DF7CB

wuxx, 2025-06-25:
Hello, can you try replacing the stepper motor driver for testing? Currently, we are using A4988, and there should be many alternative models on the market. So far, no other customers have reported interference issues

Ricapar, 2025-08-02:
I have some faraday cloth and tape on-order, I'll report back on if it helps or not!

Ricapar, 2025-08-26:
Following up on this one… I tried a few things:

* Wrapped the wires in faraday tape.
* Put as many ferrite chokes as I could fit on the wire while still being able to move.
* Draped a faraday blanket over the whole thing.

I still get overwhelming amounts of noise whenever the servos are plugged in. The noise is definitely coming from the servos.

Any ideas? Suggestions?

wuxx, 2025-08-26:
Hello, could you try wrapping the motor with electromagnetic shielding tape

sm7duz-lab, 2025-08-26:
Try a 100 uF capacitor between VMOT and GND. Short leads.

Den tis 26 aug. 2025 02:37wuxx ***@***.***> skrev:

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

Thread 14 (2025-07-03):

是否能提供完整的3D打印零件图纸？

TerayTech, 2025-07-03:
非常感谢您的开源项目！
我正尝试制作一个类似的转台用于测试天线辐射图测量，

在尝试制作时我发现：
在structure文件夹中仅有L-Bracket-42-v12.STL 和Rotator-Bottom-v02.STL两个文件，分别是一个L型支架以及底部圆盘

请问能否分享下其他的零件？或者能否指点下如何获取其他的完整的零部件文件？这对于构建完整的转台至关重要

wuxx, 2025-08-26:
你好，目前是暂时不提供的，非常抱歉

Closed 2025-08-26.

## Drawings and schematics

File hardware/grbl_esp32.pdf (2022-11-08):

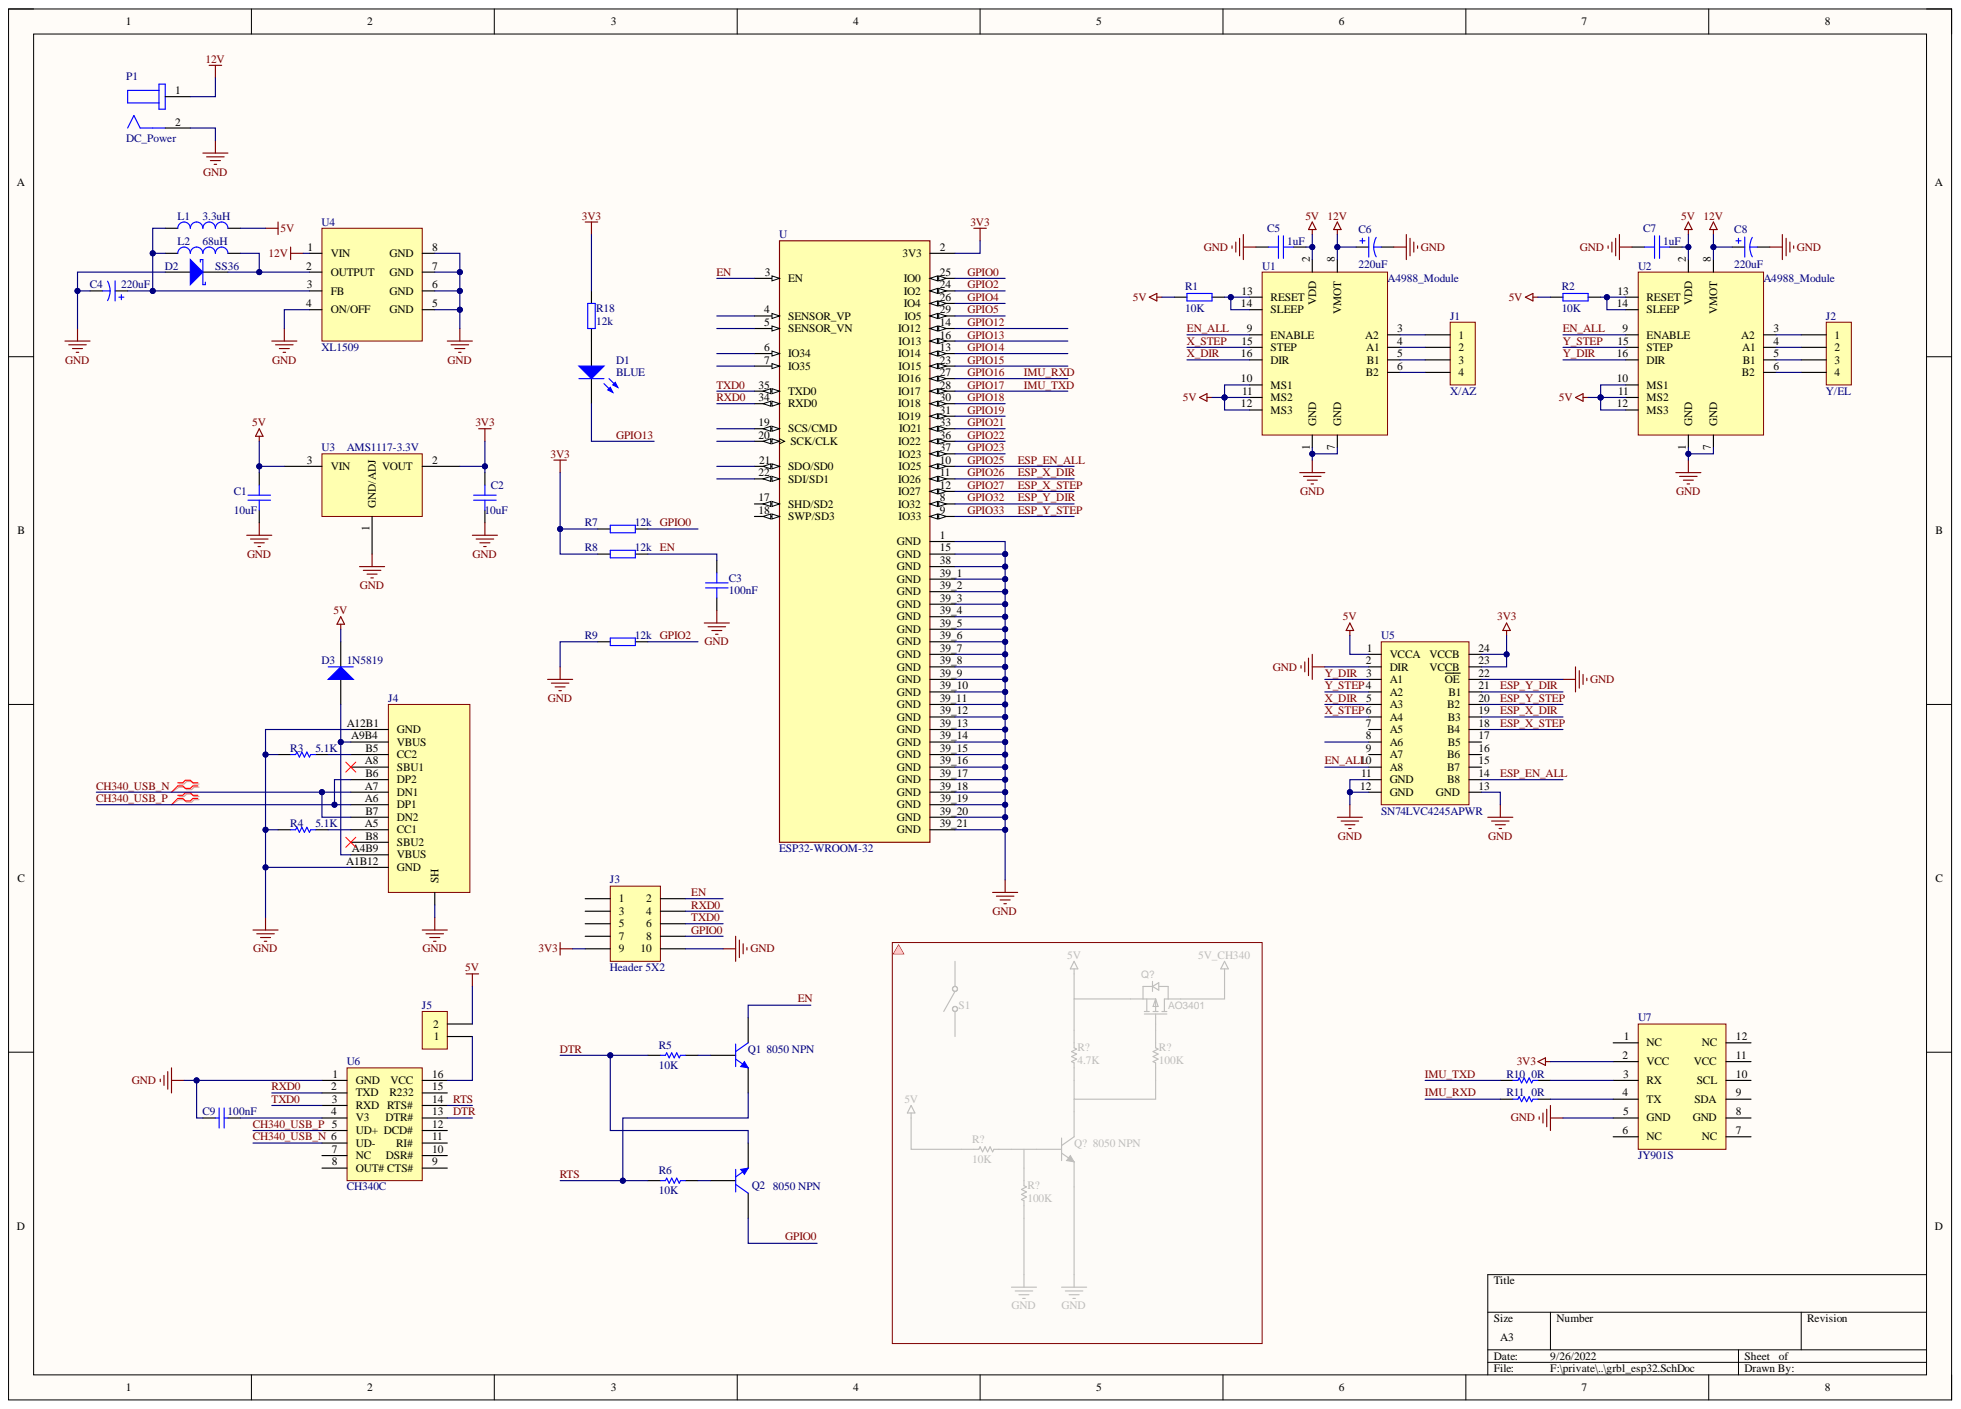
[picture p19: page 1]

DN1 A7
DP1 A6

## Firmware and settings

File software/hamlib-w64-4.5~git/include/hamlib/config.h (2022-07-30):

/* include/hamlib/config.h.  Generated from config.h.in by configure.  */
/* include/hamlib/config.h.in.  Generated from configure.ac by autoheader.  */

/* Frontend ABI age */
#define ABI_AGE 0

/* Frontend ABI revision */
#define ABI_REVISION 5

/* Frontend ABI version */
#define ABI_VERSION 4

/* Define to one of `_getb67', `GETB67', `getb67' for Cray-2 and Cray-YMP
   systems. This function is required for `alloca.c' support on those systems.
   */
/* #undef CRAY_STACKSEG_END */

/* Define to 1 if using `alloca.c'. */
/* #undef C_ALLOCA */

/* Define to 1 if you have `alloca', as a function or macro. */
#define HAVE_ALLOCA 1

/* Define to 1 if you have <alloca.h> and it should be used (not on Ultrix).
   */
/* #undef HAVE_ALLOCA_H */

/* Define to 1 if you have the <arpa/inet.h> header file. */
/* #undef HAVE_ARPA_INET_H */

/* Define to 1 if you have the `cfmakeraw' function. */
/* #undef HAVE_CFMAKERAW */

/* define if the compiler supports basic C++11 syntax */
#define HAVE_CXX11 1

/* Define to 1 if you have the declaration of `gai_strerror', and to 0 if you
   don't. */
#define HAVE_DECL_GAI_STRERROR 1

/* Define to 1 if you have the <dev/ppbus/ppbconf.hdev/ppbus/ppi.h> header
   file. */
/* #undef HAVE_DEV_PPBUS_PPBCONF_HDEV_PPBUS_PPI_H */

/* Define to 1 if you have the <dlfcn.h> header file. */
/* #undef HAVE_DLFCN_H */

/* Define to 1 if you have the <errno.h> header file. */
#define HAVE_ERRNO_H 1

/* Define to 1 if you have the <fcntl.h> header file. */
#define HAVE_FCNTL_H 1

/* Define to 1 if you have the `floor' function. */
#define HAVE_FLOOR 1

/* Define to 1 if you have the <gd.h> header file. */
/* #undef HAVE_GD_H */

/* Define to 1 if you have the `getaddrinfo' function. */
#define HAVE_GETADDRINFO 1

/* Define to 1 if you have the `getopt' function. */
#define HAVE_GETOPT 1

/* Define to 1 if you have the <getopt.h> header file. */
#define HAVE_GETOPT_H 1

/* Define to 1 if you have the `getopt_long' function. */
#define HAVE_GETOPT_LONG 1

/* Define to 1 if you have the `getpagesize' function. */
#define HAVE_GETPAGESIZE 1

/* Define to 1 if you have the `gettimeofday' function. */
#define HAVE_GETTIMEOFDAY 1

/* Define to 1 if you have the `glob' function. */
/* #undef HAVE_GLOB */

/* Define to 1 if you have the <glob.h> header file. */
/* #undef HAVE_GLOB_H */

/* Define to 1 if you have the <history.h> header file. */
/* #undef HAVE_HISTORY_H */

/* Define to 1 if you have the `inet_ntoa' function. */
/* #undef HAVE_INET_NTOA */

/* Define to 1 if you have the <inttypes.h> header file. */
#define HAVE_INTTYPES_H 1

/* Define to 1 if you have the `ioctl' function. */
/* #undef HAVE_IOCTL */

/* Define to 1 if you have the <lauxlib.h> header file. */
/* #undef HAVE_LAUXLIB_H */

/* Define if you have an INDI compatible library */
/* #undef HAVE_LIBINDI */

/* Define if you have a nova compatible library */
/* #undef HAVE_LIBNOVA */

/* Define if you have a readline compatible library */
/* #undef HAVE_LIBREADLINE */

/* Define if libusb-1.0 is available */
#define HAVE_LIBUSB 1

/* Define to 1 if you have the <libusb-1.0/libusb.h> header file. */
#define HAVE_LIBUSB_1_0_LIBUSB_H 1

/* Define to 1 if you have the <libusb.h> header file. */
/* #undef HAVE_LIBUSB_H */

/* Define to 1 if you have the <limits.h> header file. */
#define HAVE_LIMITS_H 1

/* Define to 1 if you have the <linux/hidraw.h> header file. */
/* #undef HAVE_LINUX_HIDRAW_H */

/* Define to 1 if you have the <linux/ioctl.h> header file. */
/* #undef HAVE_LINUX_IOCTL_H */

/* Define to 1 if you have the <linux/parport.h> header file. */
/* #undef HAVE_LINUX_PARPORT_H */

/* Define to 1 if you have the <linux/ppdev.h> header file. */
/* #undef HAVE_LINUX_PPDEV_H */

/* Define to 1 if you have the <locale.h> header file. */
#define HAVE_LOCALE_H 1

/* Define to 1 if you have the <luaconf.h> header file. */
/* #undef HAVE_LUACONF_H */

/* Define to 1 if you have the <lualib.h> header file. */
/* #undef HAVE_LUALIB_H */

/* Define to 1 if you have the <lua.h> header file. */
/* #undef HAVE_LUA_H */

/* Define to 1 if you have the <malloc.h> header file. */
#define HAVE_MALLOC_H 1

/* Define to 1 if you have the `memchr' function. */
#define HAVE_MEMCHR 1

/* Define to 1 if you have the `memmove' function. */
#define HAVE_MEMMOVE 1

/* Define to 1 if you have the <memory.h> header file. */
#define HAVE_MEMORY_H 1

/* Define to 1 if you have the `memset' function. */
#define HAVE_MEMSET 1

/* Define to 1 if you have the `nanosleep' function. */
#define HAVE_NANOSLEEP 1

/* Define to 1 if you have the <netdb.h> header file. */
/* #undef HAVE_NETDB_H */

/* Define to 1 if you have the <netinet/in.h> header file. */
/* #undef HAVE_NETINET_IN_H */

/* Define to 1 if you have the `pow' function. */
#define HAVE_POW 1

/* Define if you have POSIX threads libraries and header files. */
#define HAVE_PTHREAD 1

/* Define to 1 if you have the <pthread.h> header file. */
#define HAVE_PTHREAD_H 1
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

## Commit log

2022-11-23 Add more details about control system
    More notes in "Rotator Motor Control" section of README about WiFi and Grbl.
    (English version only, sorry only know a little Chinese just from Duolingo not enough to talk about G-Code and Azimuth 😄 )
2022-11-23 Small additions to Hamlib section
    Mostly to add notes that AntRunner (aka grbltrk) support was first released in Hamlib 4.5
2022-11-24 On branch master Your branch is up-to-date with 'origin/master'.
    Changes to be committed:
    deleted: doc/IMG_7510.jpeg
    new file: hardware/grbl_esp32.pdf
    modified: software/hamlib-w64-4.5~git/AntRunner_Start_Serial.bat
    new file: structure/L-Bracket-42-v1.2.STL
    new file: structure/Rotator-Bottom-v0.2.STL
    [L-Bracket-42-v1.2.STL, Rotator-Bottom-v0.2.STL]
2022-11-24 On branch master Your branch is up-to-date with 'origin/master'.
    new file: software/Grbl_Esp32-master.zip
    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
2025-03-19 add CH340 driver
